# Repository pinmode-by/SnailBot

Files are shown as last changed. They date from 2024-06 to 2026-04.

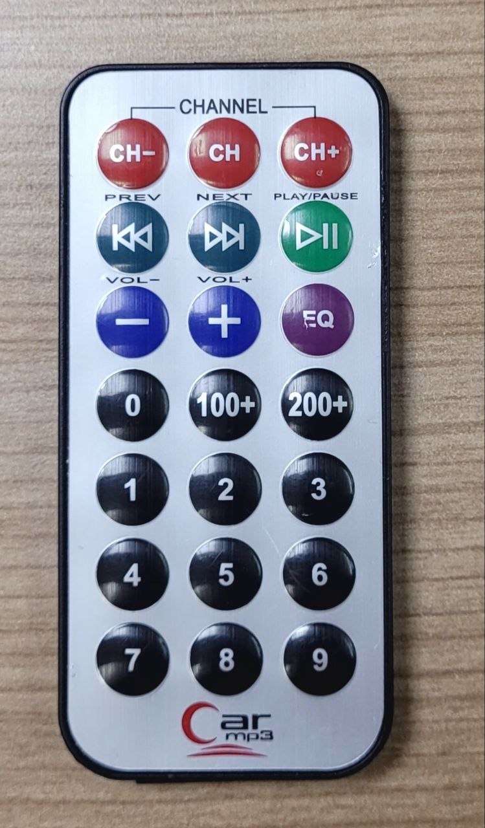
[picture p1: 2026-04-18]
Hardware/IR RC control.jpg

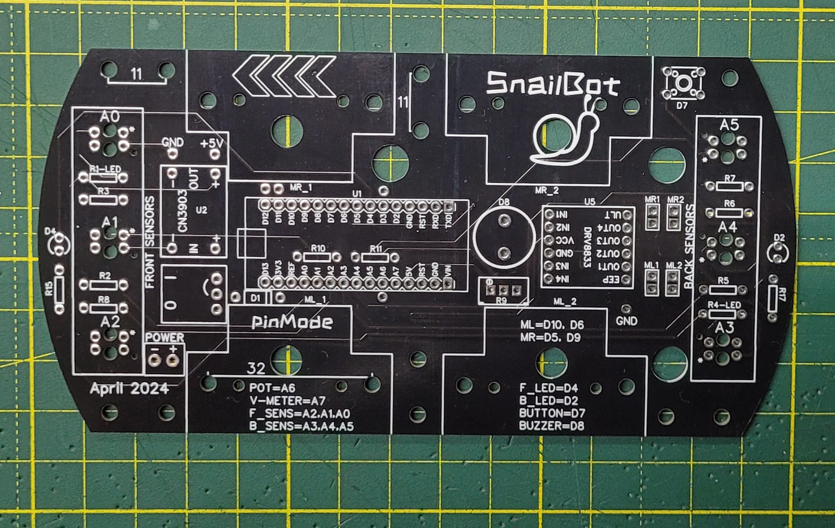
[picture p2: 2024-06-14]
Hardware/SnailBot_20240614_153012.jpg

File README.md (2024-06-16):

**SnailBot** - робот, двигающийся по линии от метки к метке и создающий препятствие для других роботов.

Такой вид робота используется в категории соревнований "**Большое путешествие. Старшие**".

В роботе предполагается использование 4 колес, привод осуществляется от 2 или 4 коллекторных моторов постоянного тока.

**Основные детали:**
* Управляющая плата: Arduino nano
* Драйвер моторов: DRV8833 - 1шт.
* Оптопары: TCRT5000 - 6 шт.
* Стабилизатор напряжения: CN93 (5V)

**Особенности:**
 * Все детали выводные
 * Имеется защита от переполюсовки питания
 * Потенциометр для регулировки параметров робота
 * Измеритель питающего напряжения
 * Звуковая и световая индикация
 * Возможность использования различных типов моторов

SnailBot is open project of active obstacle robot.

SnailBot is developed in pinMode club, Minsk, Belarus

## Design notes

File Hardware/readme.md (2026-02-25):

Питание робота - 6-9 Вольт, подходит 2S LiPo аккумуляторы или 2 элемента 18650

Элементы управления:
- Кнопка -1 шт для запуска/калибровки робота
- Светодиоды - 2шт для указания направления движения, подачи информации о состоянии робота
- Динамик - 1 шт звуковых сообщений

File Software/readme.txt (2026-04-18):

Holik_bot - Код для старая версии робота, в 2021-2024 работавшем на соревнованиях. (Arduino Uno + L298 + 6 цифровых датчиков линии)

SnailBot - Новый робот, выполненный на собственной печатной плате, разработанной учениками клуба pinMode. (Arduino nano + DRV8833 + 6 аналоговых датчиков)

SnailBot_IR_control - Управление роботом с помощью ИК пульта: старт, стоп, калибровка, скорость+, скорость-

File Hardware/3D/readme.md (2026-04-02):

SnailBot_horn.stl - Передняя/задняя поддержка - 2шт. Также необходимо напечатать зеркальную копию - 2шт.

SnailBot_side_support - Боковые поддержки - 2шт

SnailBot_18650_box - Коробка для источника питания - 1шт.

Bracket_N20_enforced - Усиленная скобка для моторов типоразмера N20

***.stl - Колесо - 4шт.

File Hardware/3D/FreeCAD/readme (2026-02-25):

Исходные файлы в формате FreeCAD. Можно редактировать.

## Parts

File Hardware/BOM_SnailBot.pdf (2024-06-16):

ID | Name | Designator | Footprint | Quantity | Manufacturer Part
1 | TCRT5000L | CGQ1,CGQ2,CGQ3,CGQ4,CGQ5,CGQ6 | OPTO-TH_TCRT5000L | 6 | TCRT5000L
2 | XT30UPB-M | CN1 | CONN-TH_XT30UPB-M | 1 | XT30UPB-M
3 | 1N5818RLG | D1 | DO-41_BD2.4-L4.7-P8.70-D0.9-RD | 1 | 1N5818RLG
4 | K4-6×6_TH | KEY1 | KEY-TH_4P-L6.0-W6.0-P4.50-LS6.5 | 1 | K2-1102DP-E4SW-04
5 | LED-TH-3mm_B | LED2 | LED-TH_BD3.0_BLUE | 1 | 204-10SUBC/S400-A4
6 | LED-TH-3mm_R | LED3 | LED-TH_BD3.0_RED | 1 | 204-10SDRD/S530-A3-L
7 | CONN-TH_2P-P2.54 | | | 4
8 | Power | P4 | HDR-3X1/2.54 | 1 | Header2.54mm 1*3P
9 | 100 | R1,R4 | R_AXIAL-0.3 | 2
10 | 10k | R2,R3,R5,R6,R7,R8,R10 | R_AXIAL-0.3 | 7
11 | 4k7 | R11 | R_AXIAL-0.3 | 1
12 | 470 | R12 | AXIAL-0.3 | 1
13 | 1K | R14 | AXIAL-0.3 | 1
14 | R_3386P_EU | RP1 | RES-ADJ-TH_3386P | 1
15 | BUZZER | SG1 | BUZZER-12MM-NS-KIT | 1
16 | ARDUINO_NANO | U1 | COMM-TH_ARDUINO_NANO | 1 | ARDUINO_NANO
17 | CN3903-DCDC | U2 | CN3903 DCDC | 1
18 | DRV8833 | U5 | DRV8833 (NO ORIGINAL) | 1

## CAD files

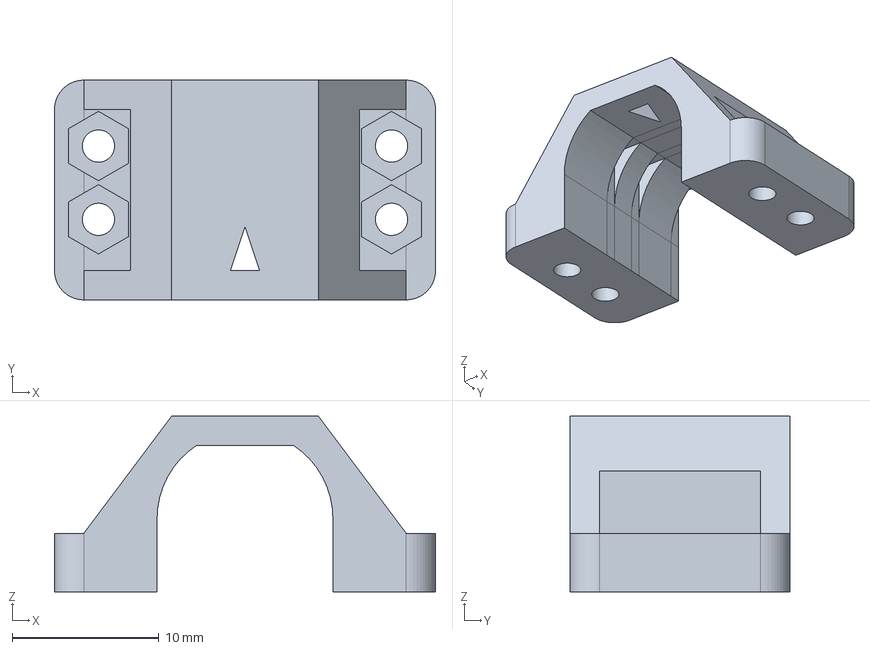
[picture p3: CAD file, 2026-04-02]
Hardware/3D/FreeCAD/Bracket_N20_enforced.FCStd
26.0 x 15.0 x 12.0 mm

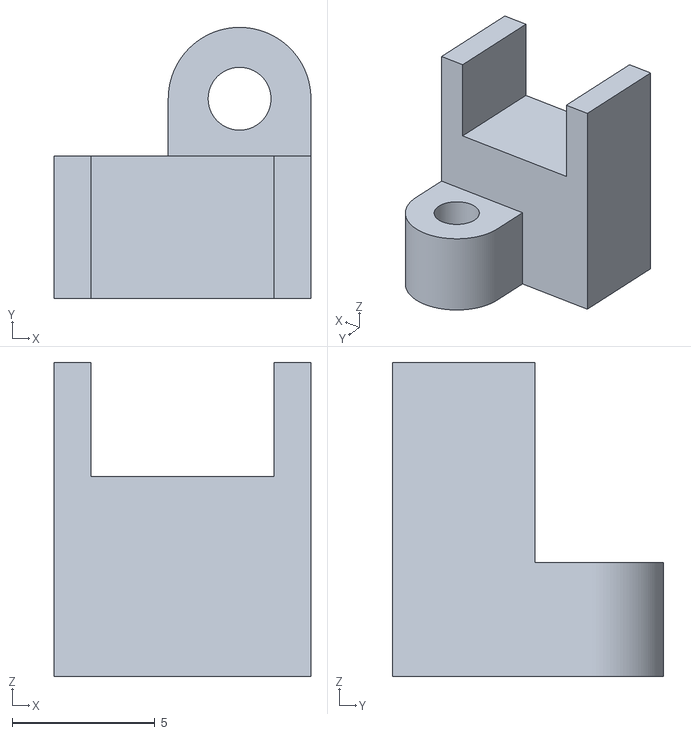
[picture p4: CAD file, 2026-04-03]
Hardware/3D/TSOP_support.stl
9.00 x 9.50 x 11.0

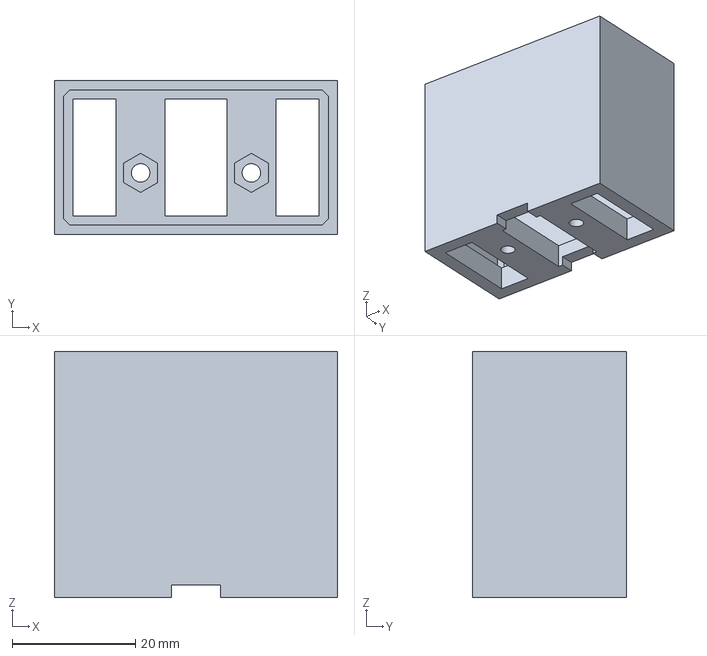
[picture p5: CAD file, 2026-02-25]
Hardware/3D/FreeCAD/SnailBot_18650_box.FCStd
46.0 x 25.0 x 40.0 mm

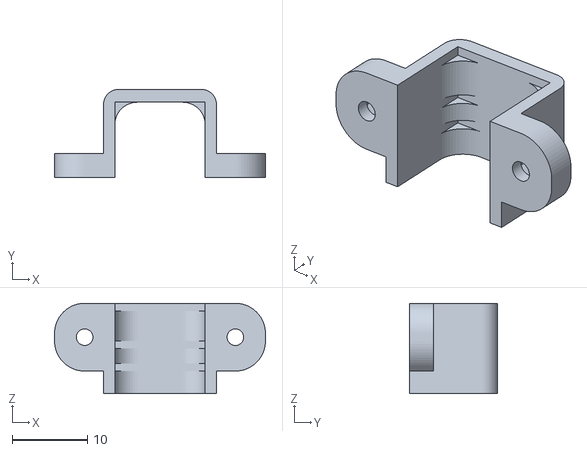
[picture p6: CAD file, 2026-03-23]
Hardware/3D/n20_motor_bracket.stl
28.0 x 11.7 x 12.0

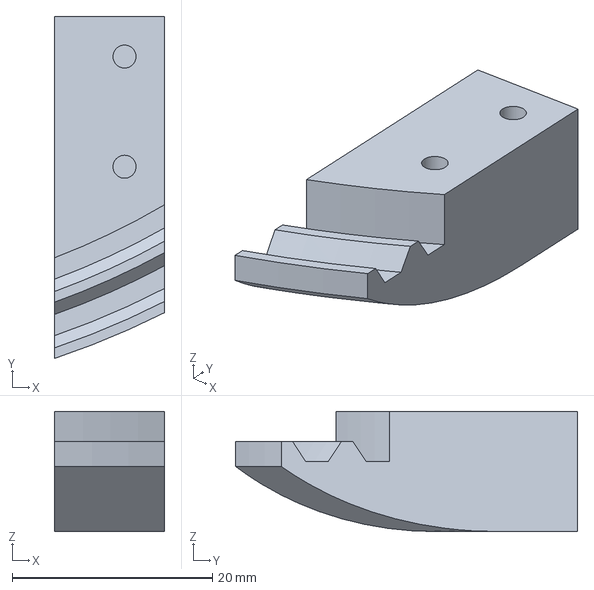
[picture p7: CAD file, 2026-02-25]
Hardware/3D/FreeCAD/SnailBot_horn.FCStd
11.0 x 34.1 x 12.0 mm

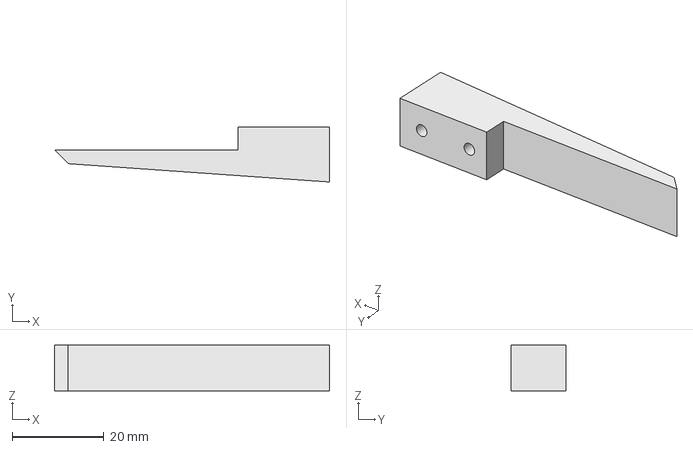
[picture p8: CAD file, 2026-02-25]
Hardware/3D/FreeCAD/snailBot_side_support.FCStd
60.0 x 12.0 x 10.0 mm

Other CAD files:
Hardware/3D/Bracket_N20_enforced.stl
Hardware/3D/SnailBot_18650_box.stl
Hardware/3D/SnailBot_horn.stl
Hardware/3D/snailBot_side_support.stl

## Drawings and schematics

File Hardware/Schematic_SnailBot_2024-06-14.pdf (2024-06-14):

## Front sensors

## LED

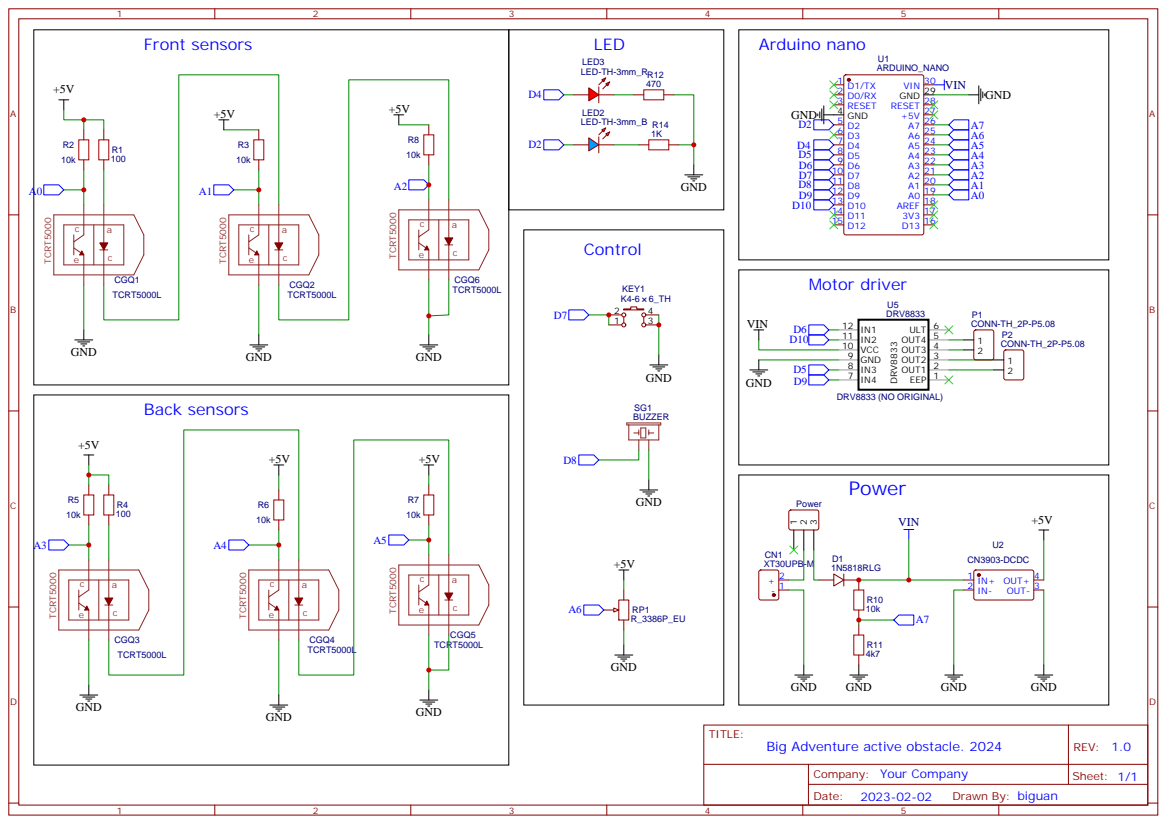
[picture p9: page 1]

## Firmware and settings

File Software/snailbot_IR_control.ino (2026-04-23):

// SnailBot
// active obstacle robot
// arduino nano + DRV8833(black) + 6*TCRT5000
// IR remote control
// Auto voltage level correction

#include <Arduino.h>
#include <IRremote.hpp>
#include <EEPROM.h>

// pinout:
const byte BUTTON = 7;   //start/stop buton
const byte FLED = 4;     // front LED pin
const byte BLED = 2;     // back LED pin
const byte BUZZ = 8;     //active buzzer
const byte POT = A6;     //potentiometer pin
const byte VMETER = A7;  //voltage meter pin, 8.0V =500, kV=0.0160
const byte ML1 = 10;     //left motor pin1
const byte ML2 = 6;      //left motor pin2
const byte MR1 = 9;      //right motor pin1
const byte MR2 = 5;      //right motor pin2
const byte IR_PIN = 12;  //IR remote TSOP pin

// IR remote codes:
const unsigned long IR_START = 0xBC43FF00;       // PLAY
const unsigned long IR_STOP = 0xBA45FF00;        // CH-
const unsigned long IR_CALIBR = 0xF609FF00;      // EQ
const unsigned long IR_SPEED_UP = 0xEA15FF00;    // +
const unsigned long IR_SPEED_DOWN = 0xF807FF00;  // -

enum Command {
  cmdLFR,
  cmdStop,
  cmdCalibr,
  cmdPlus,
  cmdMinus,
  cmdNo
};

String COM_STR[] = { "RUN", "STOP", "CALIBR", "PLUS", "MINUS", "" };

int state = 0;       //state of robot, 0-stop, 1-forward, -1 - back
int speed = 80;      //default robot speed
const int V8 = 500;  // 8V power source
const int MINSPEED = 40;
const int MAXSPEED = 160;
const int NUMSENS = 6;
const int START_DELAY = 300;
const int SPEED_ADR = 190;
const int CALIBR_ADR = 200;

int sensorPins[NUMSENS] = { A2, A1, A0, A5, A4, A3 };
int sensor[NUMSENS];  //sensor values
int maxSens[NUMSENS];
int minSens[NUMSENS];

int th[NUMSENS] = { 300, 300, 300, 300, 300, 300 };  //threshold for each sensor

// function
void readSensors();
byte digitLine();
void calibration(int cycles);
void readCalibration();
void printSensors();
void drive(int left, int right);
void LFR();
void loadEEPROM();
void saveEEPROM();
void plusSpeed();
void minusSpeed();
void printCommand(int com);


void printCommand(int com) {
  Serial.println(COM_STR[com]);
}

void plusSpeed() {
  speed = speed + 5;
  if (speed > MAXSPEED) speed = MAXSPEED;
  saveEEPROM();
  delay(200);
}

void minusSpeed() {
  speed = speed - 5;
  if (speed < MINSPEED) speed = MINSPEED;
  saveEEPROM();
  delay(200);
}

void saveEEPROM() {
  EEPROM.put(SPEED_ADR, speed);
}

void loadEEPROM() {
  int s;
  EEPROM.get(SPEED_ADR, s);
  if ((s < 0)) {
    speed = 80;
  } else speed = s;
}

void readSensors() {
  for (int i = 0; i < NUMSENS; i++) {
    sensor[i] = analogRead(sensorPins[i]);  //+ analogRead(sensorPins[i])) / 2;
  }
}

byte digitLine() {
  byte sum = 0B00000000;
  byte w = 0B00000001 << (NUMSENS - 1);
  for (int j = 0; j < NUMSENS; j++) {
    if (sensor[j] > th[j]) sum = sum + w;
    w = w / 2;
  }
  return sum;
}

void calibration(int cycles) {
  for (int j = 0; j < NUMSENS; j++) {
    minSens[j] = 1023;
    maxSens[j] = 0;
  }
  drive(80, -80);
  for (int i = 0; i < cycles; i++) {
    readSensors();
    digitalWrite(FLED, (i / 500) % 2);
    digitalWrite(BLED, !((i / 500) % 2));
    for (int j = 0; j < NUMSENS; j++) {
      if (sensor[j] > maxSens[j]) maxSens[j] = sensor[j];
      if (sensor[j] < minSens[j]) minSens[j] = sensor[j];
    }
  }
  drive(0, 0);
  int adr = CALIBR_ADR;
  for (int j = 0; j < NUMSENS; j++) {
    th[j] = (minSens[j] + maxSens[j]) / 2;
    EEPROM.put(adr, th[j]);
    adr = adr + sizeof(th[j]);
    Serial.print(th[j]);
    Serial.print("  ");
  }
  Serial.println();
  digitalWrite(FLED, LOW);
  digitalWrite(BLED, LOW);
}

void readCalibration() {
  int adr = CALIBR_ADR;
  int val;
  for (int j = 0; j < NUMSENS; j++) {
    EEPROM.get(adr, val);
    if (isnan(val) || (val > 1000) || (val < 0)) {
      th[j] = 300;
    } else {
      th[j] = val;
    }
    adr = adr + sizeof(th[j]);
  }
}

void printSensors() {
  for (int i = 0; i < NUMSENS; i++) {
    Serial.print(sensor[i]);
    Serial.print("  ");
  }
  Serial.print(" => ");
  Serial.print(digitLine(), BIN);
  Serial.print("  V= ");
  Serial.println(analogRead(VMETER));
}

void drive(int left, int right) {
  int v = analogRead(VMETER);    //voltage
  left = (long)left * V8 / v;    //voltage correction of left motor
  right = (long)right * V8 / v;  //voltage correction of right  motor
  left = constrain(left, -255, 255);
  right = constrain(right, -255, 255);
  if (left > 0) {
    analogWrite(ML1, left);
    digitalWrite(ML2, 0);
  } else if (left < 0) {
    analogWrite(ML2, -left);
    digitalWrite(ML1, 0);
  } else {
    digitalWrite(ML1, 1);
    digitalWrite(ML2, 1);
  }

  if (right > 0) {
    analogWrite(MR1, right);
    digitalWrite(MR2, 0);
  } else if (right < 0) {
    analogWrite(MR2, -right);
    digitalWrite(MR1, 0);
  } else {
    digitalWrite(MR1, 1);
    digitalWrite(MR2, 1);
  }
}


int getCmdIR() {
  int retCmd = cmdNo;
  if (IrReceiver.decode()) {
    switch (IrReceiver.decodedIRData.decodedRawData) {
      case IR_START:
        retCmd = cmdLFR;
        break;
      case IR_STOP:
        retCmd = cmdStop;
        break;

      case IR_CALIBR:
        retCmd = cmdCalibr;
        break;
      case IR_SPEED_UP:
        retCmd = cmdPlus;
        break;
      case IR_SPEED_DOWN:
        retCmd = cmdMinus;
        break;
    }
    IrReceiver.resume();
  }
  return retCmd;
}

void LFR() {
  byte cmd;
  while (1) {
    cmd = getCmdIR();
    if (cmd != cmdNo) {
      printCommand(cmd);
    }
    switch (cmd) {
      case cmdLFR:
        digitalWrite(FLED, HIGH);
        delay(START_DELAY);
        state = 1;
        LFR();
        break;
      case cmdStop:
        drive(0, 0);
        state = 0;
        return;
      case cmdPlus:
        plusSpeed();
        break;
      case cmdMinus:
        minusSpeed();
        break;
    }


    if (state == 0) {
      cmd = getCmdIR();
      if (cmd != cmdNo) {
        printCommand(cmd);
      }

      if (cmd == cmdLFR) state = 1;
      readSensors();
      printSensors();
      delay(200);

    } else if (state == 1) {
      digitalWrite(FLED, HIGH);
      digitalWrite(BLED, LOW);
      readSensors();
      byte DL = digitLine() >> 3;

      if (DL == 0B010 || DL == 0B111) {
        digitalWrite(FLED, LOW);
        drive(speed, speed);
      } else if (DL == 0B100) {
        // digitalWrite(FLED, HIGH);
        drive(speed * 1.4, speed * 0.6);
      } else if (DL == 0B110) {
        // digitalWrite(FLED, HIGH);
        drive(speed * 1.2, speed * 0.8);
      } else if (DL == 0B001) {
        // digitalWrite(FLED, HIGH);
        drive(speed * 0.6, speed * 1.4);
      } else if (DL == 0B011) {
        // digitalWrite(FLED, HIGH);
        drive(speed * 0.8, speed * 1.2);
      } else if (DL == 0B000 || DL == 0B101) {
        // digitalWrite(FLED, HIGH);
        drive(0, 0);
        state = -1;
      }
    }

    else if (state == -1) {
      digitalWrite(FLED, LOW);
      digitalWrite(BLED, HIGH);
      readSensors();
      byte DL = digitLine() & 0B00000111;
      if (DL == 0B010 || DL == 0B111) {
        digitalWrite(BLED, LOW);
        drive(-speed, -speed);
      } else if (DL == 0B100) {
        //digitalWrite(BLED, HIGH);
        drive(-speed * 0.6, -speed * 1.4);
      } else if (DL == 0B110) {
        //digitalWrite(BLED, HIGH);
        drive(-speed * 0.8, -speed * 1.2);
      } else if (DL == 0B001) {
        // digitalWrite(BLED, HIGH);
        drive(-speed * 1.4, -speed * 0.6);
      } else if (DL == 0B011) {
        // digitalWrite(BLED, HIGH);
        drive(-speed * 1.2, -speed * 0.8);
      } else if (DL == 0B000 || DL == 0B101) {
        //digitalWrite(BLED, HIGH);
        drive(0, 0);
        state = 1;
      }
    }
  }
}

void setup() {
  Serial.begin(9600);
  pinMode(FLED, OUTPUT);
  pinMode(BLED, OUTPUT);
  pinMode(BUZZ, OUTPUT);
  pinMode(ML1, OUTPUT);
  pinMode(ML2, OUTPUT);
  pinMode(MR1, OUTPUT);
  pinMode(MR2, OUTPUT);
  pinMode(BUTTON, INPUT_PULLUP);
  pinMode(IR_PIN, INPUT);
  IrReceiver.begin(IR_PIN, ENABLE_LED_FEEDBACK);
  delay(500);
  loadEEPROM();
  readCalibration();

  digitalWrite(FLED, LOW);
  digitalWrite(BLED, LOW);

  Serial.print("Speed=");
  Serial.println(speed);
  readSensors();
  printSensors();
}

void loop() {
  if (!digitalRead(BUTTON)) {
    digitalWrite(FLED, HIGH);
    delay(START_DELAY);
    state = 1;
    LFR();
    digitalWrite(FLED, LOW);
  }

  byte cmd = cmdNo;
  cmd = getCmdIR();
  if (cmd != cmdNo) {
    printCommand(cmd);
  }
  switch (cmd) {
    case cmdLFR:
      digitalWrite(FLED, HIGH);
      delay(START_DELAY);
      state = 0;
      LFR();
      digitalWrite(FLED, LOW);
      break;
    case cmdCalibr:
      calibration(10000);
      break;
  }
}

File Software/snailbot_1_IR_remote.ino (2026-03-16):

// SnailBot
// active obstacle robot
// arduino nano + DRV8833(black) + 6*TCRT5000
// Control with IRremote
#include <IRremote.hpp>

const int BUTTON = 7;   //start/stop buton
const int FLED = 4;     // front LED pin
const int BLED = 2;     // back LED pin
const int BUZZ = 8;     //active buzzer
const int POT = A6;     //potentiometer pin
const int VMETER = A7;  //voltage meter pin
const int ML1 = 10;     //left motor pin1
const int ML2 = 6;      //left motor pin2
const int MR1 = 9;      //right motor pin1
const int MR2 = 5;      //right motor pin2
const int IR_PIN = 12;  // IR remote pin (TSOP4038)

const unsigned long IR_START = 0xF9067984;      // HOME
const unsigned long IR_STOP = 0xED127984;       // POWER
const unsigned long IR_CALIBR = 0xF00F7984;     // SEARCH
const unsigned long IR_READ_SENS = 0xF50A7984;  // PLAY
const unsigned long IR_TEST = 0xF7087984;       // ENTER
const unsigned long IR_INFO = 0xE51A7984;       // OPTION

enum Command {
  cmdLFR,
  cmdStop,
  cmdCalibr,
  cmdReadSensBT,
  cmdReadSensIR,
  cmdTest,
  cmdInfoBT,
  cmdInfoIR,
  cmdNo,
  cmdReadSensSerial
};

int state = 0;  //state of robot, 0-stop, 1-forward, -1 - back
int speed = 100;
const int MINSPEED = 80;
const int MAXSPEED = 240;
const int NUMSENS = 6;
const int START_DELAY=500;
int sensorPins[NUMSENS] = { A2, A1, A0, A5, A4, A3 };
int sensor[NUMSENS];  //sensor values
int maxSens[NUMSENS];
int minSens[NUMSENS];

int th[NUMSENS] = { 100, 100, 100, 100, 100, 100 };  //threshold for each sensor

void beep(int freq, int ms) {
  tone(BUZZ, freq);
  delay(ms);
  noTone(BUZZ);
}

int getSpeed() {  // return base robot speed
  int a = analogRead(POT);
  int v = map(a, 0, 1023, MINSPEED, MAXSPEED);
  return v;
}

void readSensors() {
  for (int i = 0; i < NUMSENS; i++) {
    sensor[i] = analogRead(sensorPins[i]);  //+ analogRead(sensorPins[i])) / 2;
  }
}
bool isCmdIR(byte cmd) {
  bool result = false;

  if (IrReceiver.decode()) {
    if (IrReceiver.decodedIRData.decodedRawData == cmd) {
      result = true;
    }
    IrReceiver.resume();
  }
  return result;
}

int getCmdIR() {
  int retCmd = cmdNo;
  if (IrReceiver.decode()) {
    unsigned long data=IrReceiver.decodedIRData.decodedRawData;

    Serial.println(data,HEX);

    switch (data) {
      case IR_START:
        retCmd = cmdLFR;
        Serial.println("LFR");
        break;
      case IR_STOP:
        retCmd = cmdStop;
        Serial.println("STOP");
        break;
      case IR_TEST:
        retCmd = cmdTest;
        Serial.println("TEST");
        break;
      case IR_CALIBR:
        retCmd = cmdCalibr;
        Serial.println("CALIBR");
        break;
      case IR_READ_SENS:
        retCmd = cmdReadSensIR;
        break;
      case IR_INFO:
        retCmd = cmdInfoIR;
        break;
    }
    IrReceiver.resume();
  }
  return retCmd;
}  //    IrReceiver.p

byte digitLine() {
  byte sum = 0B00000000;
  byte w = 0B00000001 << (NUMSENS - 1);
  for (int j = 0; j < NUMSENS; j++) {
    if (sensor[j] > th[j]) sum = sum + w;
    w = w / 2;
  }
  return sum;
}

void calibration(int cycles) {
  for (int j = 0; j < NUMSENS; j++) {
    minSens[j] = 1023;
    maxSens[j] = 0;
  }
  drive(80, -80);
  for (int i = 0; i < cycles; i++) {
    readSensors();
    for (int j = 0; j < NUMSENS; j++) {
      if (sensor[j] > maxSens[j]) maxSens[j] = sensor[j];
      if (sensor[j] < minSens[j]) minSens[j] = sensor[j];
    }
  }
  drive(0, 0);
  for (int j = 0; j < NUMSENS; j++) {
    th[j] = (minSens[j] + maxSens[j]) / 2;
    Serial.print(th[j]);
    Serial.print("  ");
  }
  Serial.println();
}


void printSensors() {
  for (int i = 0; i < NUMSENS; i++) {
    Serial.print(sensor[i]);
    Serial.print("  ");
  }
  Serial.print(" => ");
  Serial.println(digitLine(), BIN);
}

void drive(int left, int right) {
  left = constrain(left, -255, 255);
  right = constrain(right, -255, 255);
  if (left > 0) {
    digitalWrite(ML1, 1);
    analogWrite(ML2, 255 - left);
  } else {
    digitalWrite(ML2, 1);
    analogWrite(ML1, 255 + left);
  }

  if (right > 0) {
    digitalWrite(MR1, 1);
    analogWrite(MR2, 255 - right);
  } else {
    digitalWrite(MR2, 1);
    analogWrite(MR1, 255 + right);
  }
}


void setup() {
  Serial.begin(9600);
  IrReceiver.begin(IR_PIN);

  pinMode(FLED, OUTPUT);
  pinMode(BLED, OUTPUT);
  pinMode(BUZZ, OUTPUT);
  pinMode(ML1, OUTPUT);
  pinMode(ML2, OUTPUT);
  pinMode(MR1, OUTPUT);
  pinMode(MR2, OUTPUT);
  pinMode(BUTTON, INPUT_PULLUP);

  digitalWrite(FLED, HIGH);
  digitalWrite(BLED, HIGH);
  beep(440, 200);
  beep(880, 300);
  beep(1760, 400);

  delay(100);
  digitalWrite(FLED, LOW);
  digitalWrite(BLED, LOW);

  long t = millis();  // пропуск калибровки если кнопка не нажата втечении 3 сек
  while (millis() - t < 3000) {
    if (digitalRead(BUTTON) == 0) {
      calibration(10000);
    }
  }
  Serial.print("End of setup");
}

bool pressButton() {
  return !digitalRead(BUTTON);
}

void LFR() {
  digitalWrite(FLED, HIGH);
  digitalWrite(BLED, LOW);
  readSensors();
  //speed = getSpeed();
  if (state == 1) {
    byte DL = digitLine() >> 3;

    if (DL == 0B010 || DL == 0B111) {
      drive(speed, speed);
    } else if (DL == 0B100) {
      drive(speed * 1.4, speed * 0.6);
    } else if (DL == 0B110) {
      drive(speed * 1.2, speed * 0.8);
    } else if (DL == 0B001) {
      drive(speed * 0.6, speed * 1.4);
    } else if (DL == 0B011) {
      drive(speed * 0.8, speed * 1.2);
    } else if (DL == 0B000 || DL == 0B101) {
      drive(0, 0);
      state = -1;
      beep(2000, 200);
    }
  } else if (state == -1) {
    digitalWrite(FLED, LOW);
    digitalWrite(BLED, HIGH);
    readSensors();
    byte DL = digitLine() & 0B00000111;
    if (DL == 0B010 || DL == 0B111) {
      drive(-speed, -speed);
    } else if (DL == 0B100) {
      drive(-speed * 0.6, -speed * 1.4);
    } else if (DL == 0B110) {
      drive(-speed * 0.8, -speed * 1.2);
    } else if (DL == 0B001) {
      drive(-speed * 1.4, -speed * 0.6);
    } else if (DL == 0B011) {
      drive(-speed * 1.2, -speed * 0.8);
    } else if (DL == 0B000 || DL == 0B101) {
      drive(0, 0);
      state = 1;
      beep(4000, 200);
    }
  }
}

void loop() {
  byte cmd = cmdNo;
  //cmd = getCmdIR();
  //if (pressButton()) {
  //  cmd = cmdLFR;
  //}
  //if (cmd == cmdNo) {
    cmd = getCmdIR();
  //}

  switch (cmd) {
    case cmdLFR:
      digitalWrite(FLED, HIGH);
      delay(START_DELAY);
      LFR();
      digitalWrite(FLED, LOW);
      break;
    case cmdCalibr:
      calibration(10000);
      break;
    case cmdReadSensBT:
      //printSensorsBT();
      break;
    case cmdReadSensIR:
      //printSensorsSerial();
      break;
    case cmdTest:
      digitalWrite(FLED, HIGH);
      //test_drive();
      digitalWrite(FLED, LOW);
      break;
    case cmdInfoBT:
      //printInfoBT();
      break;
    case cmdInfoIR:
      //printInfoSerial();
      break;

      //...
  }  // switch
}

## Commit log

2024-06-14 Add files via upload
    PCB top
2024-06-16 Schematic PCB
2024-06-16 Top view of PCB
2025-03-31 update skip calibrate
2026-02-12 Add files via upload
    Front/back cylinder support
    [SnailBot_horn.stl]
2026-02-12 Add files via upload
    side support
    [snailBot_side_support.stl]
2026-02-12 Add files via upload
    Li-Po box
    [SnailBot_lipo_box-Тело.stl]
2026-02-25 move files
    [SnailBot_18650_box.FCStd, SnailBot_horn.FCStd, snailBot_side_support.FCStd]
2026-03-23 Bracket for N20 motor
    [n20_motor_bracket.stl]
